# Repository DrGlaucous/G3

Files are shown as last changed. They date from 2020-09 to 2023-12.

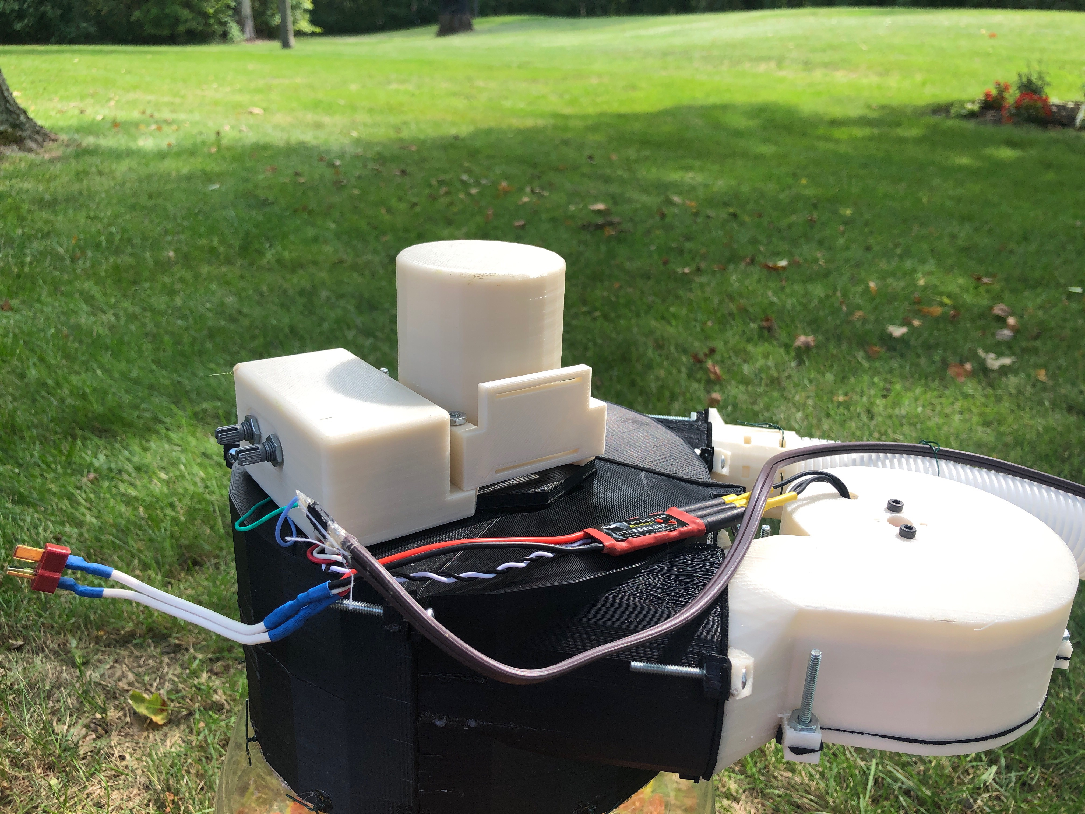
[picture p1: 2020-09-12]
CAD/Feeder Parts/Depricated/Image&Vector/2020_09_12_IMG_1746.JPG

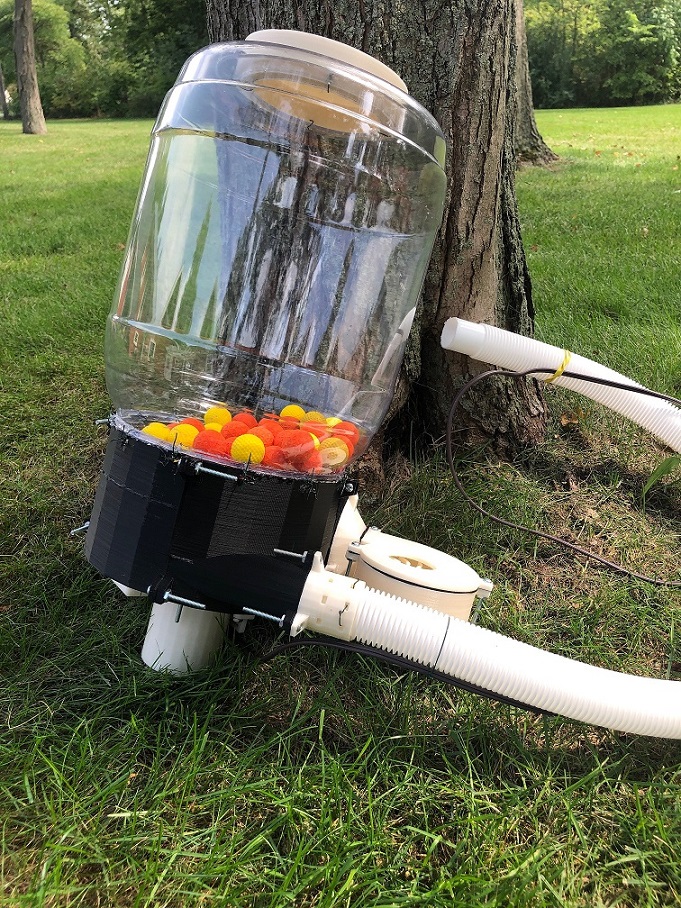
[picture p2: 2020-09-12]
CAD/Feeder Parts/Depricated/Image&Vector/ThingiverseThumbnails/2020_09_12_IMG_1745 LOWRES.jpg

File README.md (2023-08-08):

*The following is in markdown format. See the original files on thingiverse at https://www.thingiverse.com/thing:4595035/ and on github at https://github.com/DrGlaucous/G3/*

***Please use the V2 files ONLY if you want a functional SuperCell. The V1 files were my 1st attempt, and have some serious issues that have been resolved in the V2 interation. The only reason the old version is still here is for archival purposes.***  

---

After several weeks of possessing a completed prototype, I have finally had a chance to upload this to the public domain.

This device is a pressurized hopper for Nerf rival rounds (HIRs) that can be worn on the user's back and piped into a blaster of choice.

This design preforms a similar function as the ["Proton Pack"](https://outofdarts.com/products/proton-pack-hopper-feed-kit-build-it-yourself-12-5-balls-second), another pressurized round hopper designed by OutOfDarts, however, the systems used by each are designed quite differently from each other *(this is a fancy way of saying that I did not rip off OutOfDarts' design when producing this machine.)*.

My primary inspiration for the functionality of this device is stemmed from [Bui1derBB's take on the design](https://www.reddit.com/r/Nerf/comments/ckqdpb/junk_jank_proton_pack/), primarily its impeller-like agitator.

## Update 1
Version 2 has been released. This version has several important design improvements. The most important one is a smaller agitator well, allowing for faster and more reliable feeding (the agitator would bog down or even stop with fuller loads with the old design). The main section also now splits in half so that the componets at the base can be accessed without reaching all the way through the tank.

**Important note about this current iteration:** *The fan has been flipped up vertically to make room in the now smaller agitator base, and because of this, the pack is no longer ambidextrous (as of now, it is left-handed). This issue CAN be resolved simply by mirroring various pieces. I will add other files for a right-handed setup to remedy this soon)*

**Also Note:** *The agitator turbine is in need of some serious redesign. I uploaded the early prototype as it fit in this base. The agitator works, but needs lots of sanding, trial and error to do so. An updated agitator will be made avalible soon.*

## Print Settings:
The parts used for the construction are not optimized for printing, so supports will have to be used. 

I was able to print the vector on a large format printer I have access to, but if you do not have the ability to print 9x12 inch sheets, you may have to split the vector up into smaller parts

There appears to be formatting issue below. Please refer to the github page for more information.

For refrerence on how the machine should be assembled, please refer to either the exploded photograph or the source file (.skp) included with the archive. 

Electronics are mounted on a 40x70mm perfboard that fits inside the "electronics housing" model. Currently, the ESC hangs out between the brushless motor and the housing, but should remain relatively shielded if the unit is placed into a modified backpack (See the images in the archieve). 

## Required Hardware:
* Cheese ball container (used as the primary "tank". Design of this tank may be different for different regions, but it needs to have a mouth roughly 16cm in diameter. The bulk containers distributed by food manufacturer UTZ usutally fit these requirements.
* Arduino nano (or any other small microcontroller)
* 40x70mm perfboard
* Small gauge wire
* plenty of male and female (2.54mm) pin headers
* 5 volt linear regulator
* N-channel MOSFET
* 200 RPM Geartesian motor (I used [this one](https://www.amazon.com/Greartisan-Electric-Reduction-Centric-Diameter/dp/B072R57C56) , but other variants can be used, too. ***Please note that you may have to tweak the motor housing if one of the [offset motors](https://www.amazon.com/Torque-Reversible-Gear-Box-Electric-Replacement/dp/B00T47CKL2) are used***)
* 2205 variant brushless motor and 20-30a ESC (I suggest that [Racestar V1](https://m.racerstar.com/racerstar-racing-edition-2205-br2205-2300kv-2-4s-brushless-motor-red-cw-or-ccw-for-220-250-rc-drone-fpv-racing-p-33.html) motors are used, as that is what the fan is designed around. Once again, if another type is acquired instead, you will have to redesign the fan to fit.)
* 3s LiPo battery with a high enough discharge rate to compensate for motor current draw. 
* 9x12 sheet of craft foam. (this can be any size, but you will need enough to fit all the cutouts onto it. These cutouts go between the parts to make the unit airtight and, as a result, more efficient. )
* plenty of **6-32 x 1 1/4** bolts and nuts. (they can be longer, but not shorter. Some will have to be cut to size.)
* Florist wire or similar, for securing parts. (this is used to secure many things on the pack, such as the lid and tank. In general, it is a useful item to have)

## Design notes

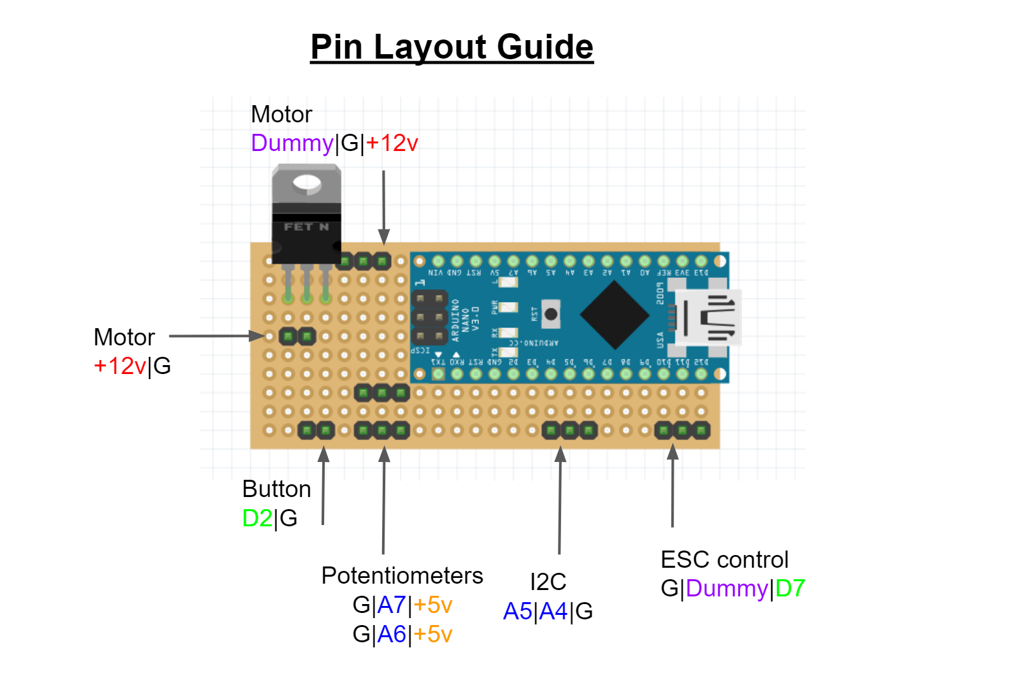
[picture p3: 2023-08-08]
Images/SuperCellPinLayout.PNG

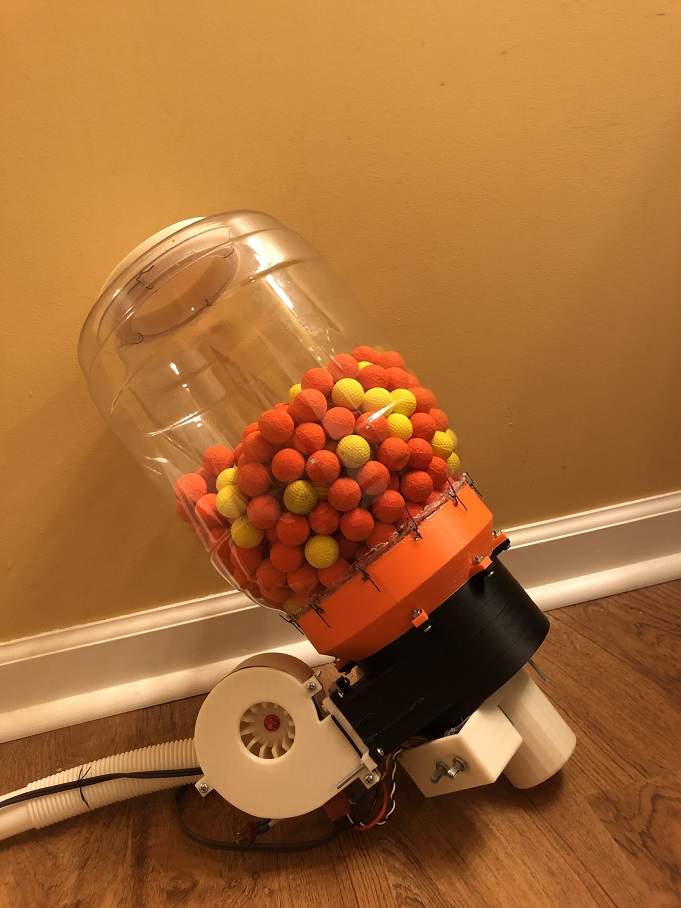
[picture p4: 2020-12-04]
Images/Image and Vector/Thingiverse Thumbnails/2020_12_03_IMG_1860_LOWRES.jpg

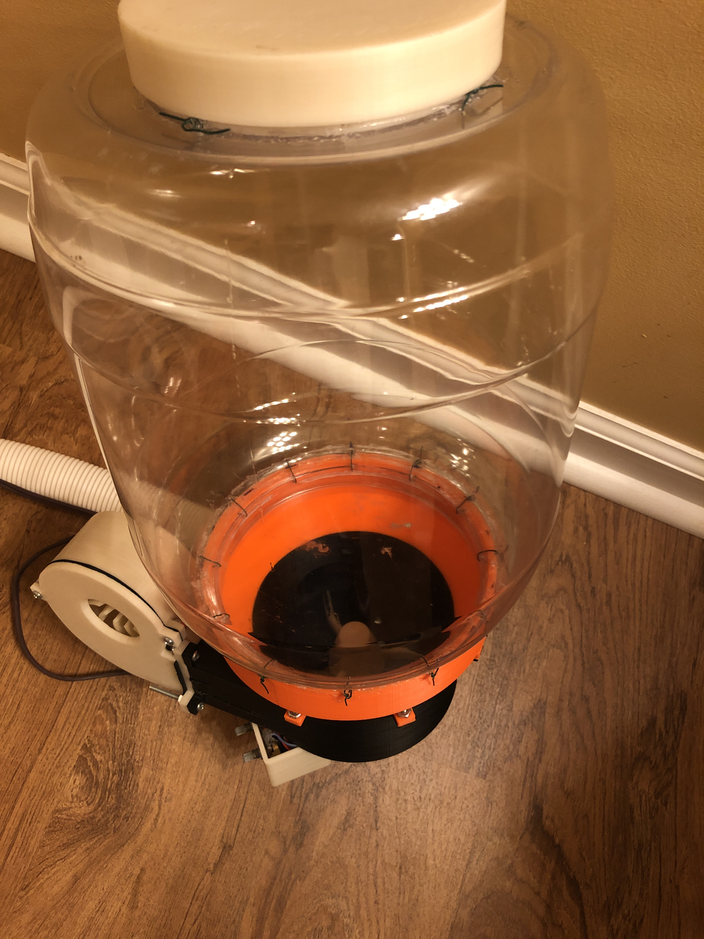
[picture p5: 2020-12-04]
Images/Image and Vector/2020_12_03_IMG_1858.JPG

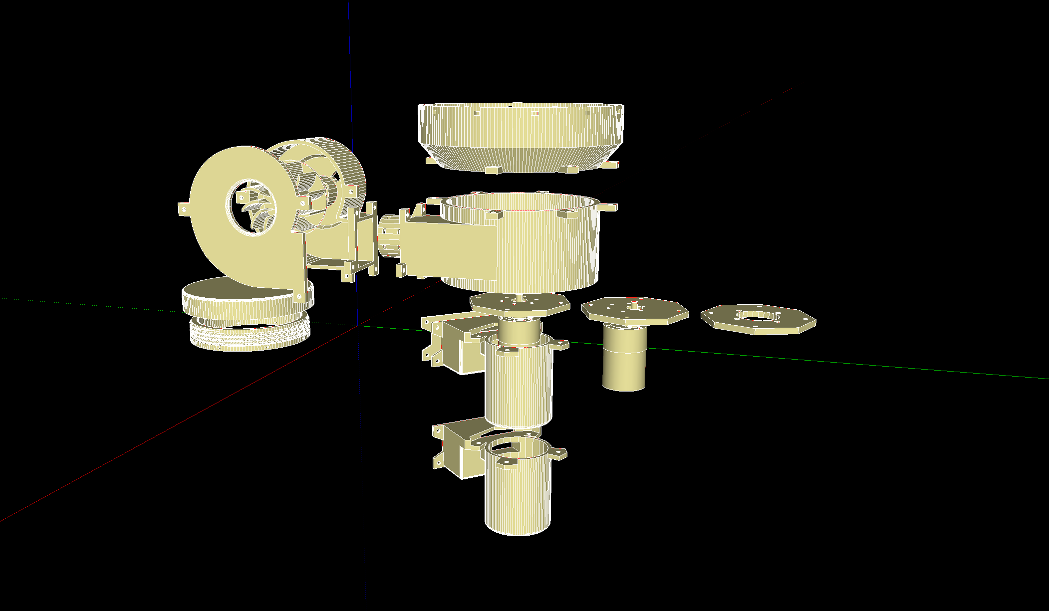
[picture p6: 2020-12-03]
Images/Image and Vector/SourcePreview.PNG

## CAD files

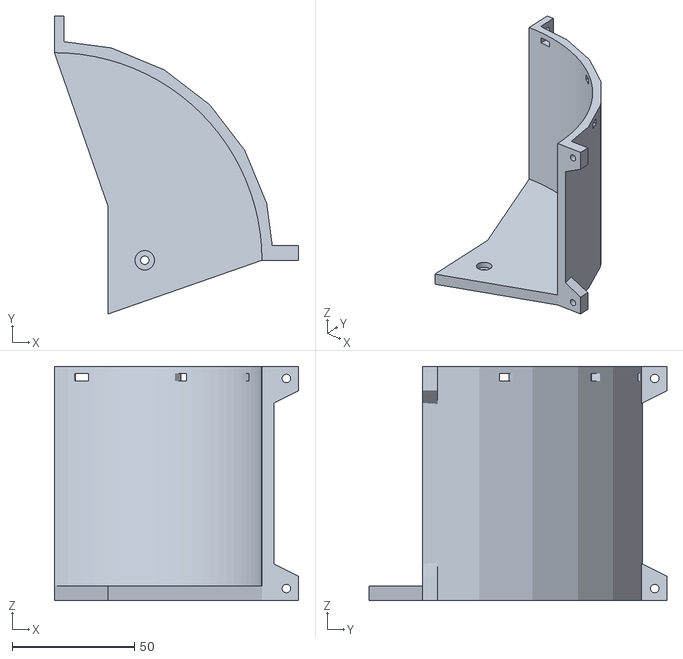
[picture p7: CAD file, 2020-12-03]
CAD/Feeder Parts/Depricated/Agitator/Main Unit Section 2.stl
100.0 x 122.0 x 96.0

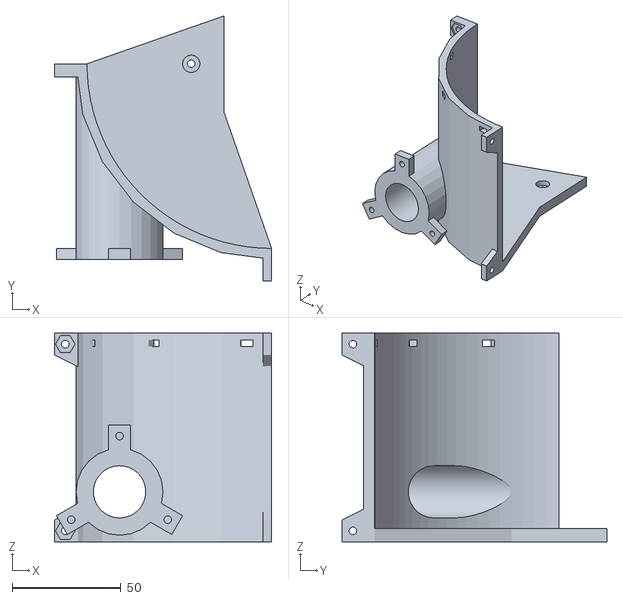
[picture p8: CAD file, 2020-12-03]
CAD/Feeder Parts/Depricated/Agitator/Main Unit Section 4 SmallBore.stl
100.0 x 122.0 x 96.0

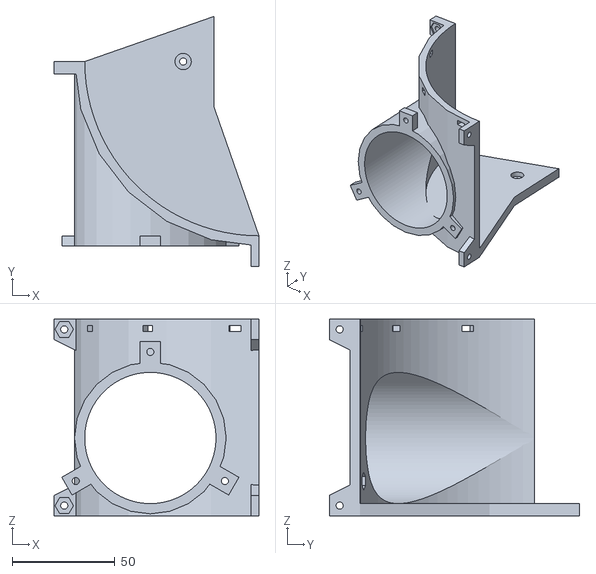
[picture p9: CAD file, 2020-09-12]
CAD/Feeder Parts/Depricated/Depricated/Main Unit Section 4[Depricated].stl
100.0 x 122.0 x 96.0

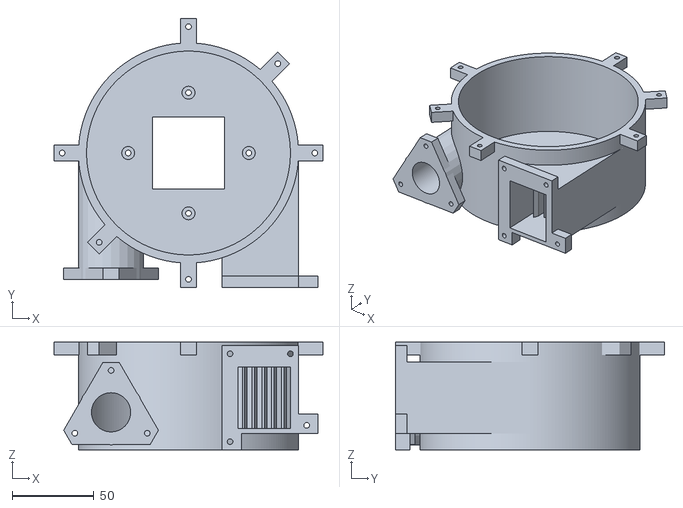
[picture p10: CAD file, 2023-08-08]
CAD/Feeder Parts/V2 (SLIM)/Agitator/Main Unit.stl
165.0 x 165.0 x 66.0

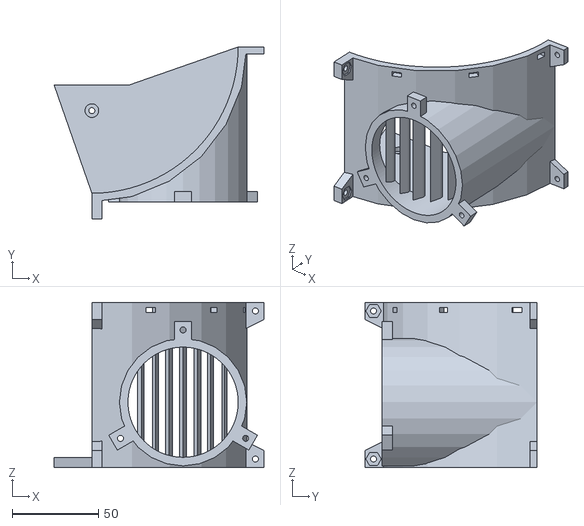
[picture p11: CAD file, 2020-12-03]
CAD/Feeder Parts/Depricated/Agitator/Main Unit Section 1.stl
122.0 x 100.0 x 96.0

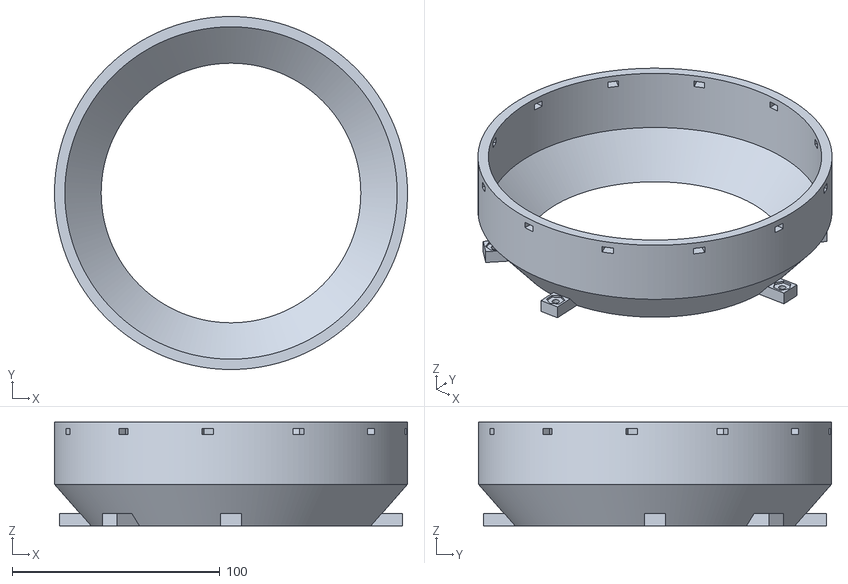
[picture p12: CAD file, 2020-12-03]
CAD/Feeder Parts/V2 (SLIM)/Agitator/Main Unit Funnel.stl
170.0 x 170.0 x 50.0

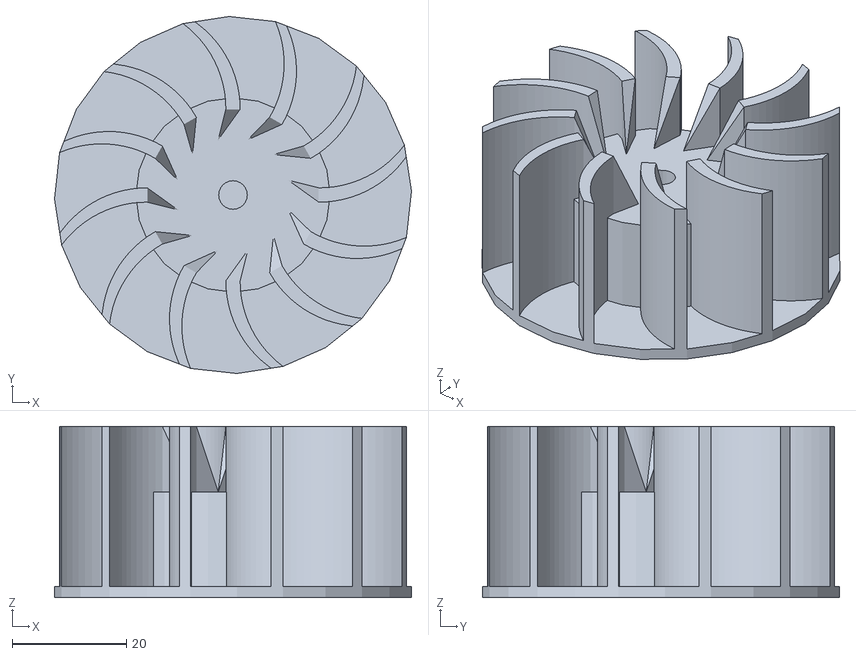
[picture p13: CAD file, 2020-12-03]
CAD/Feeder Parts/Depricated/Cfan/impeller.stl
62.5 x 62.5 x 30.0

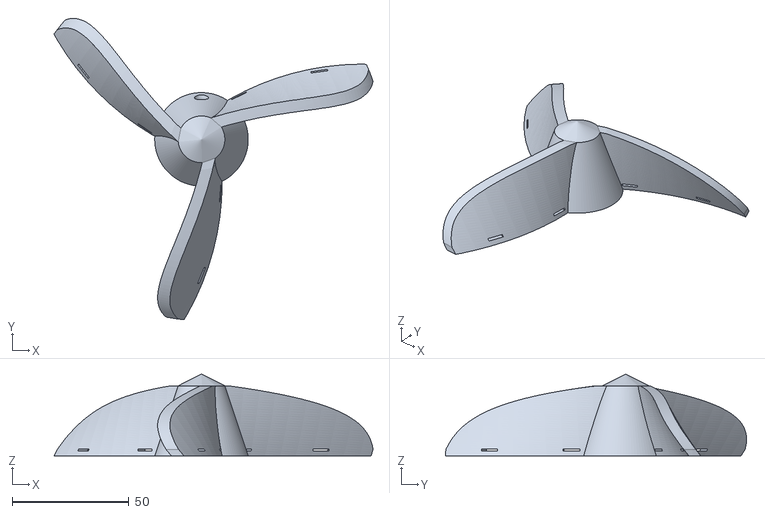
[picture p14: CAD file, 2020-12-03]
CAD/Feeder Parts/Depricated/Depricated/Agitator Brushed(6mm)[Depricated].stl
136.4 x 128.8 x 35.0

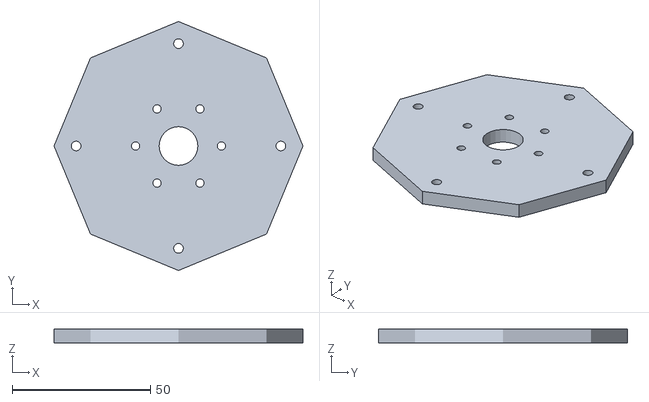
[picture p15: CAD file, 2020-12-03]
CAD/Feeder Parts/Depricated/Electronics Housing/Bottom Plate Brushed.stl
90.0 x 90.0 x 5.00

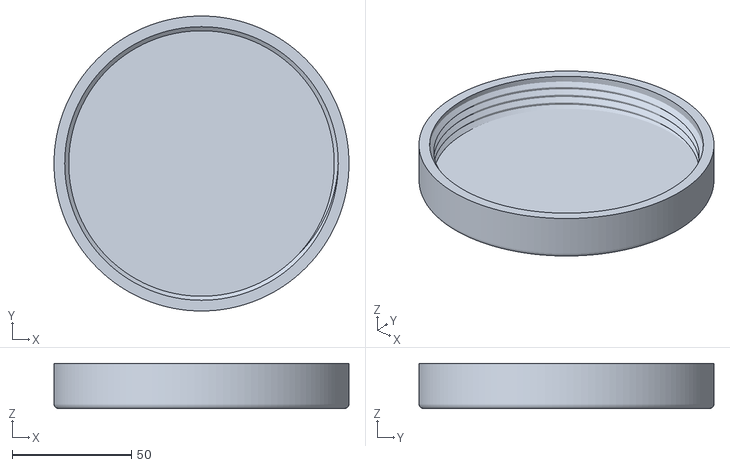
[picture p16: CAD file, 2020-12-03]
CAD/Feeder Parts/Depricated/Tank Lid/Lid Female.stl
123.8 x 123.8 x 19.0

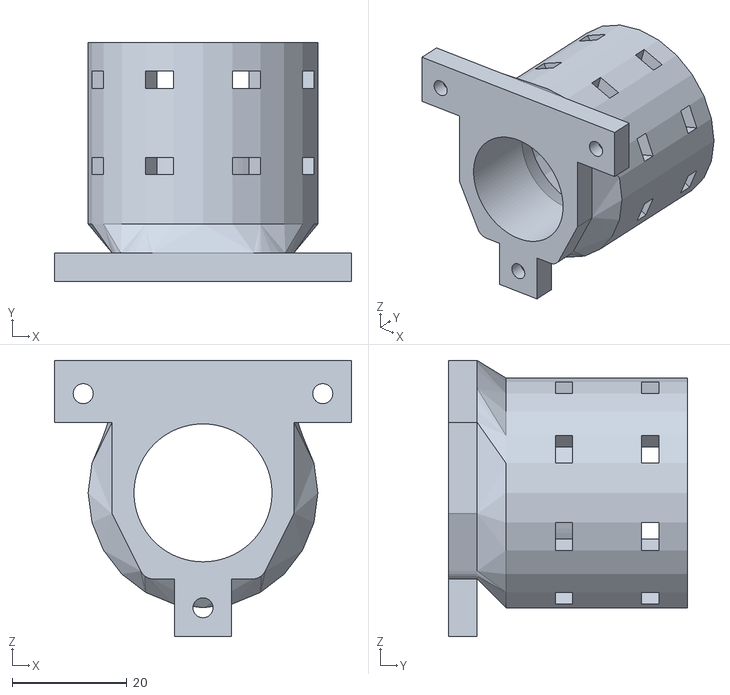
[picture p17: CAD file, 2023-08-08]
CAD/Feeder Parts/V2 (SLIM)/Agitator/Tube coupler Mag P1.stl
51.7 x 41.6 x 48.0

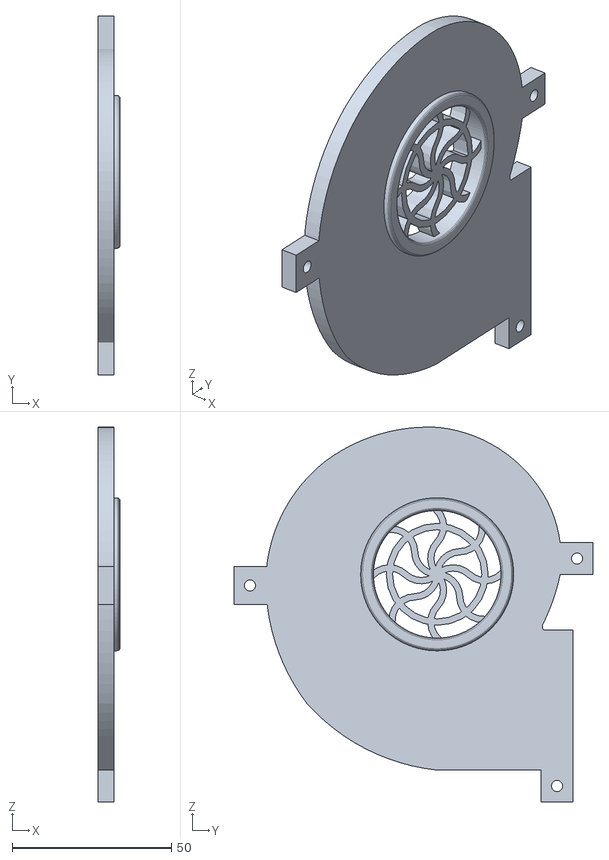
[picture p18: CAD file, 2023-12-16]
CAD/Feeder Parts/V2 (SLIM)/Cfan/ScrollLidWithGrate.stl
7.00 x 112.6 x 117.6

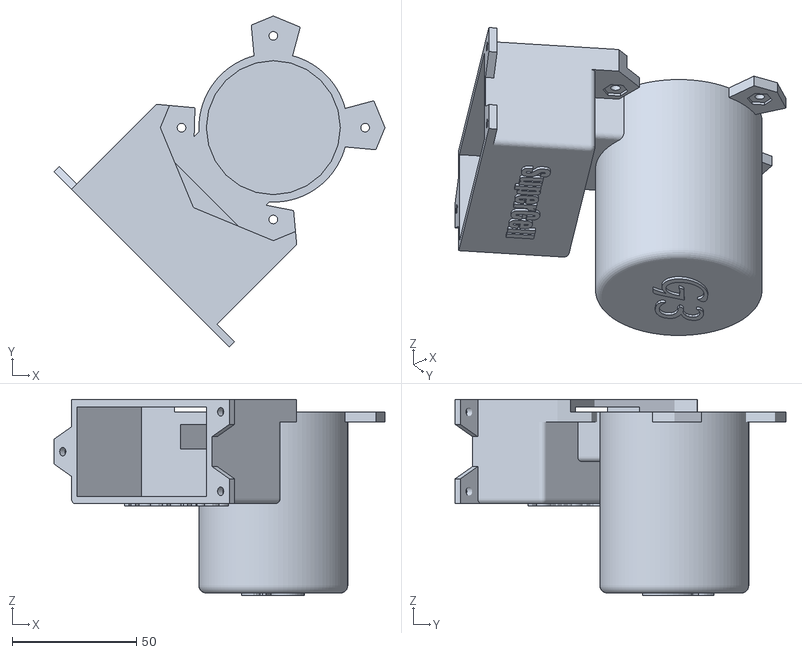
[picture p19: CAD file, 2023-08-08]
CAD/Feeder Parts/V2 (SLIM)/Electronics Housing/Agitator Cover Branded.stl
133.4 x 133.4 x 79.0

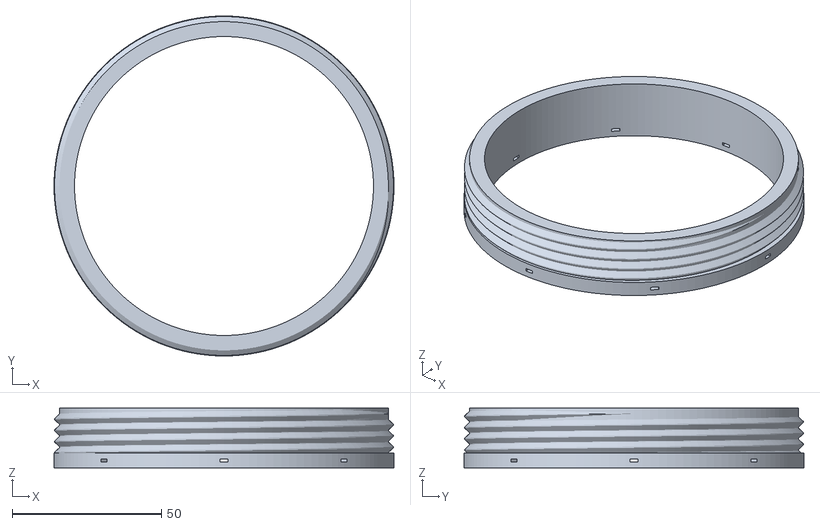
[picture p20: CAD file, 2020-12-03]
CAD/Feeder Parts/V2 (SLIM)/Tank Lid/Lid Male.stl
113.8 x 113.8 x 20.0

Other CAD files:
CAD/Feeder Parts/Depricated/Agitator/Main Unit Section 3.stl
CAD/Feeder Parts/Depricated/Cfan/ScrollLid.stl
CAD/Feeder Parts/Depricated/Electronics Housing/Bottom Plate Brushed Variant2.stl
CAD/Feeder Parts/Depricated/Tank Lid/Lid Male.stl
CAD/Feeder Parts/Depricated/Agitator/Agitator Brushed(6mm)V2.stl
CAD/Feeder Parts/Depricated/Agitator/Tube coupler.stl
CAD/Feeder Parts/Depricated/Cfan/ScrollDirectHorizontal.stl
CAD/Feeder Parts/Depricated/Depricated/Tube funnel[Depricated].stl
CAD/Feeder Parts/Depricated/Electronics Housing/Battery Strap Bracket.stl
CAD/Feeder Parts/Depricated/Electronics Housing/Bottom Plate.stl
CAD/Feeder Parts/Depricated/Electronics Housing/electronics housing EXTENDED.stl
CAD/Feeder Parts/Depricated/Electronics Housing/electronics housing.stl
CAD/Feeder Parts/V2 (SLIM)/Agitator/Agitator (SLIM) (PROTOTYPE).stl
CAD/Feeder Parts/V2 (SLIM)/Agitator/Agitator New.stl
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

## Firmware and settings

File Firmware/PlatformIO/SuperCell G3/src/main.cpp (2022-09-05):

//configuration (not enough options to warrant a completely new file)

//#define DEBUG_MODE//un-comment this to enable some serial printing of variables


#define I2C //use i2c for controlling the supercell (the supercell expects a 3-byte stream, one for on/off, one for fan, and one for Agitator speed)
#define I2C_CHANNEL 2//the channel the pack will listen on for commands
//if using an arduino nano, SCL is A5 and SDA is A4

//pin definitions
//outputs (MUST be PWM)
#define FAN_PIN 7//pin for the ESC
#define AGITATOR_PIN 3//pin for agitator motor
//inputs
#define TRIGGER_PIN 2
#define AGITATOR_POT 7
#define FAN_POT 6



#define POT_MIN_VALUE 0
#define POT_MAX_VALUE 1023

#define IDLE_ANGLE 37//(the angle that the ESC sits at when "off")
#define MAX_ANGLE 180//the angle of the ESC when it is at its fullest

#define ON_STATE 1//the state of the button when "on" (only applies when using manual control)

//end configuration


#include <Arduino.h>
#include <Servo.h>


#ifdef I2C
#include <Wire.h>
#endif

//global objects
unsigned char Angle {};//esc angle
unsigned char AgitatorSpeed {};
bool isON {};

//for the clock
unsigned long MillisecondTicks{};
unsigned long MicrosecondTicks{};
unsigned long LastMillisecondTicks{};//previous values
unsigned long LastMicrosecondTicks{};

//servo object for the fan
Servo ESCServo;


//we want a set of variables to control our blower and agitator
//3 total: blower speed, agitator speed, GO

//System clock
void GetTicks(void)
{
	LastMillisecondTicks = MillisecondTicks;
	LastMicrosecondTicks = MicrosecondTicks;

	MillisecondTicks = millis();
	MicrosecondTicks = micros();
}


//lights the onbaord LED for the desired ammount of time, run it without arguments to have it count down using the system clock
void StatusLED(int MilTime = 0, bool IsOn = false)
{
  static unsigned long EndMilTime{};

  if(IsOn == true)
  {
    EndMilTime = MillisecondTicks + MilTime;//move to end time specified
    digitalWrite(13, HIGH);//turn LED on
  }

  if(EndMilTime < MillisecondTicks)
  {
      digitalWrite(13, LOW);
  }



}


//drives the blower
void BlowerHandler(void)
{

  if(isON == ON_STATE)
  {
    ESCServo.write(Angle);
  }
  else if(ESCServo.read() > IDLE_ANGLE &&
  MillisecondTicks % 10 == 0 &&
  MillisecondTicks != LastMillisecondTicks)//once every 10 milliseconds
  {

    //decrement servo when not in use
    ESCServo.write(ESCServo.read() - 1);
  }


}

//takes the variables and drives the agitator with them
void AgitatorHandler(void)
{
  if(isON == ON_STATE)
  {
    analogWrite(AGITATOR_PIN, AgitatorSpeed);
  }
  else
  {
    analogWrite(AGITATOR_PIN, 0);
  }

}

//function that reads the pots and buttons to get the values for driving the pack
void IORead(void)
{
  //ESC
  Angle = map(analogRead(FAN_POT), POT_MIN_VALUE, POT_MAX_VALUE, IDLE_ANGLE, MAX_ANGLE);

  AgitatorSpeed = map(analogRead(AGITATOR_POT), POT_MIN_VALUE , POT_MAX_VALUE, 0, 255);

  isON = digitalRead(TRIGGER_PIN);

}

//function that gets the values from the controller device for driving the pack
#ifdef I2C
void i2cRead(int byteCount)
{
	//TODO: handle input mapping and manual control timeout

  //we should get 3 bytes: one for trigger, one for fan, and one for motor
  if(byteCount != 3)//if this is not the case, break out
  {
#ifdef DEBUG_MODE
    Serial.print("Error: Gor byte count: ");
    Serial.println(byteCount);
#endif
    return;
  }

  //should read a sequence of 3 bytes containing the needed information
  isON = Wire.read();
  Angle = map(Wire.read(), 0, 255, IDLE_ANGLE, MAX_ANGLE);
  AgitatorSpeed = Wire.read();

  StatusLED(10, true);

#ifdef DEBUG_MODE
  Serial.print(byteCount);
  Serial.print(" || ");
  Serial.print(int(isON));
  Serial.print(" : ");
  Serial.print(int(Angle));
  Serial.print(" : ");
  Serial.println(int(AgitatorSpeed));

#endif



}
#endif

void setup() {


#ifdef I2C
  Wire.begin(I2C_CHANNEL);
  Wire.onReceive(i2cRead);
#endif

  pinMode(TRIGGER_PIN, INPUT_PULLUP);
  Angle = IDLE_ANGLE;
  ESCServo.attach(FAN_PIN);
  ESCServo.write(Angle);



  //debug stuff
#ifdef DEBUG_MODE
  Serial.begin(9600);
#endif

  StatusLED(500, true);//startup blink

}

void loop() {

  GetTicks();

  //update status LED timeout
  StatusLED();

  //i2c uses callbacks, so there is no need to have it check for i2c in the mainloop
#ifndef I2C
  IORead();
#endif

  BlowerHandler();
  AgitatorHandler();




}

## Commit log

2020-12-03 File Movement
    Make way for Version 2, a more reliable and faster-feeding version than the original.
    [Agitator (SLIM) (PROTOTYPE).stl, Agitator Brushed(6mm)V2.stl, Agitator Brushed(6mm)[Depricated].stl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]
2020-12-04 More Images
    Uploaded several images of the updated pack assembly
2021-09-06 Added magazine adapter
    This is compatible with standard Nerf Rival magazine ports. It comes in 2 parts for both ease of printing and better assembly (part 1 needs to be strung to the delivery tube, and being able to access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
    [Tube coupler Mag P1.stl, Tube coupler Mag P2.stl]
2022-07-09 renamed some folders
    [Agitator Brushed(6mm)V2.stl, Agitator Brushed(6mm)[Depricated].stl, Battery Strap Bracket.stl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]
2022-07-12 Added some firmware
    Ported to the PlatformIO environment and added I2C support
2022-07-14 More firmware changes
    Should work with the G2 blaster over i2c (or in manual mode, if that's your thing)
2022-09-05 updated feedback LED
    the LED will blink each time an i2c command has been received
2023-08-08 Mesh updates
    Added thickness to some tabs that had a risk of breaking, also updated the agitator arms
    [Agitator (SLIM) (PROTOTYPE).stl, Agitator Brushed(6mm)V2.stl, Agitator Brushed(6mm)[Depricated].stl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]
2023-08-08 remove "early stage" warning.
    I've had this thing working for several years now...
2023-08-31 Add images of agitator
    The inclusion of the base plate is not explicitly defined in the readme or in any previous images. The pack is sized so that this can be made out of an old CD or DVD. I still have cardstock in mine because it hasn't failed yet, but CDs or DVDs would work better (last longer).
2023-12-16 Add grated scroll fan lid
    keeps fingers and darts out of the proton pack's fan. How did I not do this from the get-go?
    (Also, I had my pack destroyed by a dart shot into the fan)
    [ScrollLidWithGrate.stl]
